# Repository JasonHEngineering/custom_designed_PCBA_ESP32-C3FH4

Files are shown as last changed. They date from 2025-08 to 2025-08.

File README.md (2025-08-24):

# Custom PCBA design

I have designed and fabricated a custom board with ESP32-C3 with the following key hardware features:

- Using ESP32-C3FH4 (embedded flash memory)
- Power management from USB as well as from (maximum) 12 V source (LDO: AMS1117-3.3 and L78L05ABUTR)
- Stepper motor driver (DRV8825)
- Accelerometer + Gyro unit (MPU6050)
- Built-in 2.4 GHz inverted F antenna (reference)
- CAN transceiver (TJA1051T/CM,118)

Project Layout build from KiCad 6:
Refer to folder "KiCad Project Schematics and Gerbers"

## Layout snapshot



## Actual 



Scope of sample codes under folder names:
BLE_Advertising_example_V1 - BLE advertising example
BLE_Gyro_example_V2 - Gyro data sent over BLE from custom board to phone with nRF app
Custom_ESP32_DRV8825_V1 - Stepper motor driving with on board DRV8825
ESP32_custom_board_LED_flash_V1 - Initial program sanity check if the MCU is working
MP6050_trial_V2 - Grab data from gyroscope/accelrometer
SimpleWiFiServer - Becomes a web server to trigger a GPIO action (e.g. LED)
Wifi_scan_example - Scan the wifi network and check for RSSI signal strength 

## Example GIFs

InShot_20230917_184955720

InShot_20230919_152650873

InShot_20230919_204007445

InShot_20230922_123716818

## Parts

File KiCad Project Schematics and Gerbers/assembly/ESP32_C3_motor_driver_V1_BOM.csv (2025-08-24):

Comment | Designator | Footprint | LCSC
Antenna_Loop | AE1 | RF_Antenna_downloaded:2.4GHz-INVERTED-F-ANTENNA
GCM155R71C104KA55J | C1,C3,C6,C9,C13,C14,C15,C17,C18,C19,C20,C22,C23,C26,C28,C30 | 100nf_cap_GCM155R71C104KA55J:CAPC1005X55N | C84416
CL10B103KB8NNNC | C11,C25 | 10nF_cap_CL10B103KB8NNNC:CAPC1608X90N | C2655418
LMK063BC6474KPLF | C16 | 470nf_cap_LMK063BC6474KPLF:CAPC0603X39N | C91604
GRM21BR61E106KA73L | C2,C8,C12,C24 | 10uF_cap_GRM21BR61E106KA73L:CAPC2012X140N | C144384
UWT1H101MNL1GS | C21 | 100uF_cap_UWT1H101MNL1GS:PCAP_8X10-ELECT | C76906
CL05C100JB5NNNC | C27,C31 | 10pF_cap_CL05C100JB5NNNC:CAPC1005X55N | C2169138
GCM1885C1H222JA16D | C29 | 2200pF_cap_GCM1885C1H222JA16D:CAPC1608X90N | C445063
GRM31CR71A226KE15L | C4 | 22uF_cap_GRM31CR71A226KE15L:CAPC3216X180N | C1589
GCM188R71C334KA37D | C5 | 330nF_cap_GCM188R71C334KA37D:CAPC1608X90N | C343869
GJM1555C1H3R3BB01D | C7,C10 | 3p3_RF_cap_GJM1555C1H3R3BB01D:CAPC1005X55N | C32949
BAT20JFILM | D1,D2 | diode_BAT20JFILM:SOD-323 | C155590
SMD-LED-CLEAR-BLUE(0603) | D3 | Blue_LED_SMD-LED-CLEAR-BLUE_0603:LED-0603 | C72041
19-213/R6C-AP1Q2B/3T | D4 | Red_LED_19-213R6C-AP1Q2B3T:LED_19-213_R6C-AP1Q2B_3T | C128051
19-213SYGC/S530-E2/TR8 | D5 | Yellow_Green_LED_19-213SYGCS530-E2TR8:CAPC0603X39N | C409444
L78L05ABUTR | IC1 | LDO_L78L05ABUTR_5V:L78L05ABUTR | C42738
Conn_01x02_Female | J1 | Connector_JST:JST_XH_S2B-XH-A_1x02_P2.50mm_Horizontal | C157931
Conn_01x04_Female | J10 | Connector_JST:JST_XH_S4B-XH-A_1x04_P2.50mm_Horizontal | C165948
USB_C_Receptacle_USB2.0 | J2 | Connector_USB:USB_C_Receptacle_HRO_TYPE-C-31-M-12
Conn_01x04_Female | J3 | Connector_PinSocket_1.00mm:PinSocket_1x04_P1.00mm_Vertical | C173752
Conn_01x02_Female | J4,J5,J6,J8,J9 | Connector_JST:JST_PH_S2B-PH-K_1x02_P2.00mm_Horizontal | C157925
Jumper_2_Open | JP1,JP2,JP3,JP4 | solder_jumpers:SolderJumper-2_P1.3mm_Open_TrianglePad1.0x1.5mm
LQW15AN2N2G80D | L1,L2 | 2n2_RF_inductor_LQW15AN2N2G80D:INDC1006X60N | C412264
TC33X-2-103E | R11 | 10k_pot_TC33X-2-103E:TRIM_TC33X-2-103E | C114758
RL1206JR-070R2L | R12,R13 | 200mR_RL1206JR-070R2L:RESC3116X65N | C169259
RC0402FR-075K1L | R2,R3,R6,R10,R14,R15,R16,R22,R23,R27 | 5.1kR_RC0402FR-075K1L:RESC1005X40N | C719176
ERJ3EKF1004V | R21 | 1MR_ERJ3EKF1004V:RES_ERJ3EKF1004V | C327155
AC0402FR-0722RL | R24 | 22R_AC0402FR-0722RL:RESC1005X37N | C105872
RC0402FR-07120RL | R4 | 120R_RC0402FR-07120RL:RESC1005X40N | C193390
ERJ3EKF4700V | R5,R17,R18,R19,R20 | 470R_ERJ3EKF4700V:RES_ERJ3EKF4700V | C226359
TS-1187A-B-A-B | S1,S2 | Tact_switch_TS-1187A-B-A-B:SW_TS-1187A-B-A-B | C318884
TestPoint | TP1 | TestPoint:TestPoint_Pad_2.0x2.0mm
TJA1051T/CM,118 | U1 | CAN_tranceiver_TJA1050T_CM_118:SOIC127P600X175-8N | C2859133
AMS1117-3.3 | U2 | LDO_AMS1117-3v3:SOT229P700X180-4N | C6186
USBLC6-2SC6 | U3 | Package_TO_SOT_SMD:SOT-23-6 | C7519
DRV8825PWPR | U4 | stepper_driver_DRV8825.pretty:IC_TPS61196PWPRQ1 | C81582
ESP32-C3FH4 | U6 | ESP32-C3FH4:QFN50P500X500X90-33N | C2858491
MPU-6050 | U7 | Sensor_Motion:InvenSense_QFN-24_4x4mm_P0.5mm | C24112
40MHz 9pF ±10ppm SMD3225-4P | Y1 | crystal_footprints:Crystal_SMD_SeikoEpson_TSX3225-4Pin_3.2x2.5mm | C255943

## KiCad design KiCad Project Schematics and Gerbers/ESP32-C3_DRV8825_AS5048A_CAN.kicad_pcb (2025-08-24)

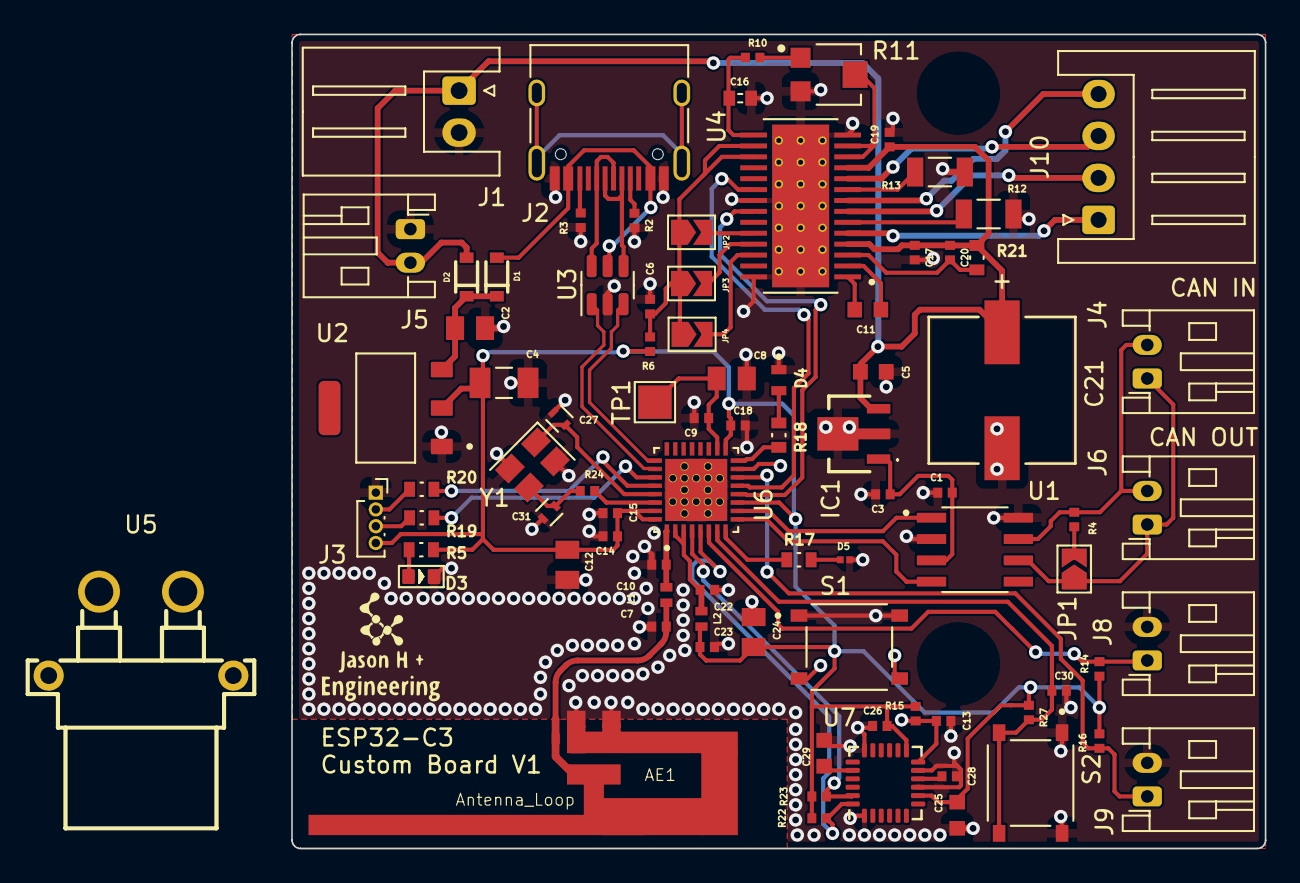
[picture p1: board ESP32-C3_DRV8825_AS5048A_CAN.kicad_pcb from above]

Board: 4 copper layers, 58.0 x 48.5 mm, 85 parts (0 on the bottom side), 59 nets.

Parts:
AE1: Antenna_Loop; 2.4GHz-INVERTED-F-ANTENNA
C1, C3, C6, C9, C13, C14, C15, C17, C18, C19, C20, C22, C23, C26, C28, C30: GCM155R71C104KA55J; CAPC1005X55N
C2, C8, C12, C24: GRM21BR61E106KA73L; CAPC2012X140N
C4: GRM31CR71A226KE15L; CAPC3216X180N
C5: GCM188R71C334KA37D; CAPC1608X90N
C7, C10: GJM1555C1H3R3BB01D; CAPC1005X55N
C11, C25: CL10B103KB8NNNC; CAPC1608X90N
C16: GRM155B31A474KE14D; INDC1005X45
C21: 100uF; PCAP_8X10-ELECT
C27, C31: CL10C100JB8NNNC; CAPC1005X55N
C29: GCM1885C1H222JA16D; CAPC1608X90N
D1, D2: BAT20JFILM; SOD-323
D3: SMD-LED-CLEAR-BLUE(0603); LED-0603
D4: 19-213/R6C-AP1Q2B/3T; LED_19-213_R6C-AP1Q2B_3T
D5: SZYY0402W; CAPC0603X39N
IC1: L78L05ABUTR
J1: Conn_01x02_Female; JST_XH_S2B-XH-A_1x02_P2.50mm_Horizontal
J2: USB_C_Receptacle_USB2.0; USB_C_Receptacle_HRO_TYPE-C-31-M-12
J3: Conn_01x04_Female; PinSocket_1x04_P1.00mm_Vertical
J4, J5, J6, J8, J9: Conn_01x02_Female; JST_PH_S2B-PH-K_1x02_P2.00mm_Horizontal
J10: Conn_01x04_Female; JST_XH_S4B-XH-A_1x04_P2.50mm_Horizontal
JP1, JP2, JP3, JP4: Jumper_2_Open; SolderJumper-2_P1.3mm_Open_TrianglePad1.0x1.5mm
L1, L2: LQW15AN2N2G80D; INDC1006X60N
R2, R3, R6, R10, R14, R15, R16, R22, R23, R27: RC0402FR-075K1L; RESC1005X40N
R4: RC0402FR-07120RL; RESC1005X40N
R5, R17, R18, R19, R20: ERJ3EKF4700V; RES_ERJ3EKF4700V
R11: TC33X-2-103E; TRIM_TC33X-2-103E
R12, R13: RL1206JR-070R2L; RESC3116X65N
R21: ERJ3EKF1004V; RES_ERJ3EKF1004V
R24: AC0402FR-0722RL; RESC1005X37N
S1, S2: TS-1187A-B-A-B; SW_TS-1187A-B-A-B
TP1: TestPoint; TestPoint_Pad_2.0x2.0mm
U1: TJA1051T/CM,118; SOIC127P600X175-8N
U2: AMS1117-3.3; SOT229P700X180-4N
U3: USBLC6-2SC6; SOT-23-6
U4: DRV8825PWPR; IC_TPS61196PWPRQ1
U5: XT30PW-F; CONN-TH_XT30PW-F-1
U6: ESP32-C3FH4; QFN50P500X500X90-33N
U7: MPU-6050; InvenSense_QFN-24_4x4mm_P0.5mm
Y1: 40MHz 9pF ±10ppm SMD3225-4P; Crystal_SMD_SeikoEpson_TSX3225-4Pin_3.2x2.5mm

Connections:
/3V3: C4.1, C12.1, C14.1, C15.1, C18.1, C23.1, C24.1, C25.1, C26.1, J3.4, L2.2, R5.1, R6.1, R14.1, R15.1, R16.1, R22.1, R23.1, R27.1, U2.2 (VOUT), U6.11 (VDD3P3_RTC), U6.17 (VDD3P3_CPU), U6.31 (VDDA), U6.32 (VDDA), U7.8 (VDDIO), U7.13 (VDD)
/3v3_ref: C16.1, R10.1, U4.15 (V3P3OUT)
/5V_CAN: C1.1, C3.1, IC1.1 (VOUT), U1.3 (VCC)
/5V_USB: D1.A, J2.A4 (VBUS), J2.A9 (VBUS), J2.B4 (VBUS), J2.B9 (VBUS), U3.5 (VBUS)
/12V: C5.1, C17.1, C19.1, C20.1, C21.1, D2.A, IC1.3 (VIN), J1.1, J5.2, R21.1, U4.4 (VMA), U4.11 (VMB)
/+3V3_RF: C22.1, L2.1, U6.2 (VDD3P3), U6.3 (VDD3P3)
/Antenna: C10.1, L1.2, U6.1 (LNA_IN)
/CAN_H: J4.2, J6.2, R4.2, U1.7 (CANH)
/CAN_L: J4.1, J6.1, JP1.1 (A), U1.6 (CANL)
/CAN_RX_N: U1.4 (RXD), U6.9 (MTMS)
/CAN_TX_P: U1.1 (TXD), U6.10 (MTDI)
/DIR: U4.20 (DIR), U6.13 (MTDO)
/INT_ACC: C13.1, R15.2, S1.C, S1.D, U6.15 (GPIO9), U7.12 (INT)
/LED1: R17.1, U6.8 (GPIO3)
/LED2: R18.1, U6.16 (GPIO10)
/M11: J10.1, U4.5 (AOUT1)
/M12: J10.2, U4.7 (AOUT2)
/M13: J10.3, U4.10 (BOUT1)
/M14: J10.4, U4.8 (BOUT2)
/MC0: JP2.2 (B), U4.24 (MODE0)
/MC1: JP3.2 (B), U4.25 (MODE1)
/MC2: JP4.2 (B), U4.26 (MODE2)
/MCU_USB_D_N: U3.3 (I/O2), U6.25 (GPIO18)
/MCU_USB_D_P: U3.1 (I/O1), U6.26 (GPIO19)
/SCL_ACC: R23.2, U6.4 (XTAL_32K_P), U7.23 (SCL)
/SDA_ACC: R22.2, U6.5 (XTAL_32K_N), U7.24 (SDA)
/SET_HIGH: C6.1, JP2.1 (A), JP3.1 (A), JP4.1 (A), R6.2, U4.16 (~NRESET), U4.17 (NSLEEP)
/STP: U4.22 (STEP), U6.12 (MTCK)
/UART0_RX: J3.3, R19.2
/UART0_TX: J3.2, R20.2
/USB_D_N: J2.A7 (D-), J2.B7 (D-), U3.4 (I/O2)
/USB_D_P: J2.A6 (D+), J2.B6 (D+), U3.6 (I/O1)
/VCP: C20.2, R21.2, U4.3 (VCP)
/VDD_SPI: C8.1, C9.1, TP1.1, U6.18 (VDD_SPI)
GND: AE1.2, C1.2, C2.2, C3.2, C4.2, C5.2, C6.2, C7.2, C8.2, C9.2, C10.2, C12.2, C13.2, C14.2, C15.2, C16.2, C17.2, C18.2, C19.2, C21.2, C22.2, C23.2, C24.2, C25.2, C26.2, C27.2, C28.2, C29.2, C30.2, C31.2, D3.-, D4.1, D5.2, IC1.2 (GND_1), IC1.4 (GND_2), J1.2, J2.A1 (GND), J2.A12 (GND), J2.B1 (GND), J2.B12 (GND), J3.1, J5.1, J8.2, J9.2, R2.2, R3.2, R11.3, R12.2, R13.2, S1.A, S1.B, S2.A, S2.B, U1.2 (GND), U1.8 (S), U2.1 (GND/ADJ), U3.2 (GND), U4.14 (GND), U4.21 (NENBL), U4.28 (GND), U6.33 (GND), U7.1 (CLKIN), U7.9 (AD0), U7.11 (FSYNC), U7.18 (GND), Y1.2 (GND), Y1.4 (GND)
unnamed: AE1.1, C7.1, L1.1
unnamed: C2.1, D1.C, D2.C, U2.3 (VIN)
unnamed: C11.1, U4.1 (CP1)
unnamed: C11.2, U4.2 (CP2)
unnamed: C27.1, U6.29 (XTAL_N), Y1.1
unnamed: C28.1, U7.10 (REGOUT)
unnamed: C29.1, U7.20 (CPOUT)
unnamed: C30.1, R27.2, S2.C, S2.D, U6.7 (CHIP_EN)
unnamed: C31.1, R24.2, Y1.3
unnamed: D3.+, R5.2
unnamed: D4.2, R18.2
unnamed: D5.1, R17.2
unnamed: J2.A5 (CC1), R2.1
unnamed: J2.B5 (CC2), R3.1
unnamed: J8.1, R14.2, U6.6 (GPIO2)
unnamed: J9.1, R16.2, U6.14 (GPIO8)
unnamed: JP1.2 (B), R4.1
unnamed: R10.2, R11.1
unnamed: R11.2, U4.12 (AVREF), U4.13 (BVREF)
unnamed: R12.1, U4.6 (ISENA)
unnamed: R13.1, U4.9 (ISENB)
unnamed: R19.1, U6.27 (U0RXD)
unnamed: R20.1, U6.28 (U0TXD)
unnamed: R24.1, U6.30 (XTAL_P)

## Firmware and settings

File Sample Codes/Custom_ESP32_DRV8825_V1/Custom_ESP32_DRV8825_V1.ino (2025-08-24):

// Include the AccelStepper Library
#include <AccelStepper.h>

// Define pin connections
#define stepper_1_stepPin 6
#define stepper_1_dirPin 7


// Define motor interface type
#define motorInterfaceType 1 //AccelStepper::DRIVER (1) means a stepper driver (with Step and Direction pins)
#define no_of_steppers 1

#define movesteps 8000

//define an array of stepper pointers. initialize the pointer to NULL (null pointer) for safety (see below)
AccelStepper *steppers[no_of_steppers] = {NULL};

// Creates an instance
// AccelStepper myStepper(motorInterfaceType, stepPin, dirPin);

void setup() {

// Create stepper instances
steppers[0] = new AccelStepper(motorInterfaceType, stepper_1_stepPin, stepper_1_dirPin);

  // Configure each stepper as needed

 if (steppers[0]) {
    steppers[0]->setMaxSpeed(4000); //steps per second
    steppers[0]->setAcceleration(4000.0); //desired acceleration in steps per second per second
    steppers[0]->moveTo(movesteps);   
 }
  
 
}

void loop() {

	if (steppers[0]->distanceToGo() == 0) { 
	  // Change direction once the motor reaches target position
		steppers[0]->moveTo(-steppers[0]->currentPosition());

	}

	// Move the motor one step
	steppers[0]->run();

    
}

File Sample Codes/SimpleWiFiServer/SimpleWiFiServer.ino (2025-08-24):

#include <WiFi.h>
#define LED_1_PIN 3
#define LED_2_PIN 10

const char* ssid     = "TPMESH";
const char* password = "shaixahnge";

// Set web server port number to 80
WiFiServer server(80);

// Variable to store the HTTP request
String header;

// Auxiliar variables to store the current output state
String LED_1_PIN_State = "off";
String LED_2_PIN_State = "off";

// Current time
unsigned long currentTime = millis();
// Previous time
unsigned long previousTime = 0; 
// Define timeout time in milliseconds (example: 2000ms = 2s)
const long timeoutTime = 2000;

void setup() {
  Serial.begin(115200);
  // Initialize the output variables as outputs
  pinMode(LED_1_PIN, OUTPUT);
  pinMode(LED_2_PIN, OUTPUT);
  // Set outputs to LOW
  digitalWrite(LED_1_PIN, LOW);
  digitalWrite(LED_2_PIN, LOW);

  // Connect to Wi-Fi network with SSID and password
  Serial.print("Connecting to ");
  Serial.println(ssid);
  WiFi.begin(ssid, password);
  while (WiFi.status() != WL_CONNECTED) {
    delay(500);
    Serial.print(".");
  }
  // Print local IP address and start web server
  Serial.println("");
  Serial.println("WiFi connected.");
  Serial.println("IP address: ");
  Serial.println(WiFi.localIP());
  server.begin();
}

void loop(){
  WiFiClient client = server.available();   // Listen for incoming clients

  if (client) {                             // If a new client connects,
    currentTime = millis();
    previousTime = currentTime;
    Serial.println("New Client.");          // print a message out in the serial port
    String currentLine = "";                // make a String to hold incoming data from the client
    while (client.connected() && currentTime - previousTime <= timeoutTime) {  // loop while the client's connected
      currentTime = millis();
      if (client.available()) {             // if there's bytes to read from the client,
        char c = client.read();             // read a byte, then
        Serial.write(c);                    // print it out the serial monitor
        header += c;
        if (c == '\n') {                    // if the byte is a newline character
          // if the current line is blank, you got two newline characters in a row.
          // that's the end of the client HTTP request, so send a response:
          if (currentLine.length() == 0) {
            // HTTP headers always start with a response code (e.g. HTTP/1.1 200 OK)
            // and a content-type so the client knows what's coming, then a blank line:
            client.println("HTTP/1.1 200 OK");
            client.println("Content-type:text/html");
            client.println("Connection: close");
            client.println();
            
            // turns the GPIOs on and off
            if (header.indexOf("GET /3/on") >= 0) {
              Serial.println("GPIO 3 on");
              LED_1_PIN_State = "on";
              digitalWrite(LED_1_PIN, HIGH);
            } else if (header.indexOf("GET /3/off") >= 0) {
              Serial.println("GPIO 3 off");
              LED_1_PIN_State = "off";
              digitalWrite(LED_1_PIN, LOW);
            } else if (header.indexOf("GET /10/on") >= 0) {
              Serial.println("GPIO 10 on");
              LED_2_PIN_State = "on";
              digitalWrite(LED_2_PIN, HIGH);
            } else if (header.indexOf("GET /10/off") >= 0) {
              Serial.println("GPIO 10 off");
              LED_2_PIN_State = "off";
              digitalWrite(LED_2_PIN, LOW);
            }
            
            // Display the HTML web page
            client.println("<!DOCTYPE html><html>");
            client.println("<head><meta name=\"viewport\" content=\"width=device-width, initial-scale=1\">");
            client.println("<link rel=\"icon\" href=\"data:,\">");
            // CSS to style the on/off buttons 
            // Feel free to change the background-color and font-size attributes to fit your preferences
            client.println("<style>html { font-family: Helvetica; display: inline-block; margin: 0px auto; text-align: center;}");
            client.println(".button { background-color: #4CAF50; border: none; color: white; padding: 16px 40px;");
            client.println("text-decoration: none; font-size: 30px; margin: 2px; cursor: pointer;}");
            client.println(".button2 {background-color: #555555;}</style></head>");
            
            // Web Page Heading
            client.println("<body><h1>Jason H Engineering</h1>");
            client.println("<body><h1>Custom ESP32 board - Web Server</h1>");

            // Display current state, and ON/OFF buttons for GPIO 26  
            client.println("<p>GPIO 3 - State " + LED_1_PIN_State + "</p>");
            // If the output26State is off, it displays the ON button       
            if (LED_1_PIN_State=="off") {
              client.println("<p><a href=\"/3/on\"><button class=\"button\">ON</button></a></p>");
            } else {
              client.println("<p><a href=\"/3/off\"><button class=\"button button2\">OFF</button></a></p>");
            } 
               
            // Display current state, and ON/OFF buttons for GPIO 27  
            client.println("<p>GPIO 10 - State " + LED_2_PIN_State + "</p>");
            // If the output27State is off, it displays the ON button       
            if (LED_2_PIN_State=="off") {
              client.println("<p><a href=\"/10/on\"><button class=\"button\">ON</button></a></p>");
            } else {
              client.println("<p><a href=\"/10/off\"><button class=\"button button2\">OFF</button></a></p>");
            }
            client.println("</body></html>");
            
            // The HTTP response ends with another blank line
            client.println();
            // Break out of the while loop
            break;
          } else { // if you got a newline, then clear currentLine
            currentLine = "";
          }
        } else if (c != '\r') {  // if you got anything else but a carriage return character,
          currentLine += c;      // add it to the end of the currentLine
        }
      }
    }
    // Clear the header variable
    header = "";
    // Close the connection
    client.stop();
    Serial.println("Client disconnected.");
    Serial.println("");
  }
}

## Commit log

2025-08-24 Initial upload
    Initial upload - KiCad 6 project, schematics and gerbers
    [ESP32-C3_DRV8825_AS5048A_CAN-B_Cu.gbr, ESP32-C3_DRV8825_AS5048A_CAN-B_Mask.gbr, ESP32-C3_DRV8825_AS5048A_CAN-B_Paste.gbr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]
2025-08-24 Sample Codes Upload
    Sample Codes Upload
